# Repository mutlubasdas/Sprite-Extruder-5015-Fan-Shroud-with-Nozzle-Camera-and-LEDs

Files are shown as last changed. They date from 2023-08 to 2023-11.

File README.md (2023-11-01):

Sprite extruder is pretty good but the cooling is just not good enough!

So I did some research, got inspired by a couple of models and made my own.

Since I was making my own, I thought I make it a bit extra.

I always wanted to have a nozzle cam so I designed the shroud around it.

I'm using a [OV5640 camera](https://www.aliexpress.us/item/3256804790797706.html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) with autofocus, since that has a smaller package. The video is stable, I'm not getting any flickering, maybe I just got lucky with it :)

The focal length is more than 20mm with this camera so I used this [macro lens](<a target="_blank" href="https://www.amazon.com/gp/product/B08MFSDZB8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">Blips Macro Plus Lens</a>)* to achieve the shooting distance required! I cut it down the same size of the camera and just placed it in front of it, it sits just well because left some clearance for it in the model. Shoutout to [chilicoke](https://github.com/chilicoke) for finding that macro lens. He has an awesome [video](https://www.youtube.com/watch?v=GAp23w_dnNc&t=65s) for his own Voron nozzle camera mod.

   * I know this item has been out of stock but the seller on amazon said they'll restock in     October 2023.

    * Just checked today (11/1/23) and it's in stock right now. And created an affiliate link for the item.

There's a bracket next to the fan for the camera PCB. I used [M1.6 heatset](https://www.aliexpress.us/item/3256804538587668.html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) insert and screws to mount it.

And obviously I needed light to see what I'm printing so I added two tiny LEDs, I had extra [WS2813 LEDs](https://www.digikey.com/en/products/detail/seeed-technology-co-ltd/601000200/8120706) around so I used them but I think other models may fit also If they have similar size. Please refer to the spec sheet for details on wiring for your choice of LEDs.

Soldering was a pain the back for me! I'm not a pro at it. It took me a while and I think I killed two LEDs in the process but I eventually got it :) I also added some cable management clips on both arms of the shroud. Be gentle with them and they work, otherwise you might break them.

Finally just throw in a good 5015 fan, I got [this one](https://www.filastruder.com/products/delta-bfb0524hh-blower-fan) from Filastruder. I also made some holes that goes to the camera and the LEDs, hoping that it might help with their cooling? :) Not 100% sure how much that affects to be honest because I was lazy to test with and without them but I wanted to be safe and give them some airflow too! :) They also have holes at the bottom and they're for making disassembly easy if ever needed.

I printed with ABS, with 0.2 layer height, with a self made chamber and I used a bit of fan starting from layer 10+, which makes the print have good detail and helps with some of the small overhangs. I didn't use supports and I think you should be able to print without supports as well. Also I'd suggest considering the thermal shrinkage when printing it, I scaled my model 0.6 % in XY and %0.2 in Z. Obviously don't just copy my numbers, yours will be different depending on material, slicer settings, cooling, printer environment etc.

Anyways, enough talk, I hope some of you find it useful and make your own. It's a very dangerous project though, because once you have it working you get addicted to watching it!! :)

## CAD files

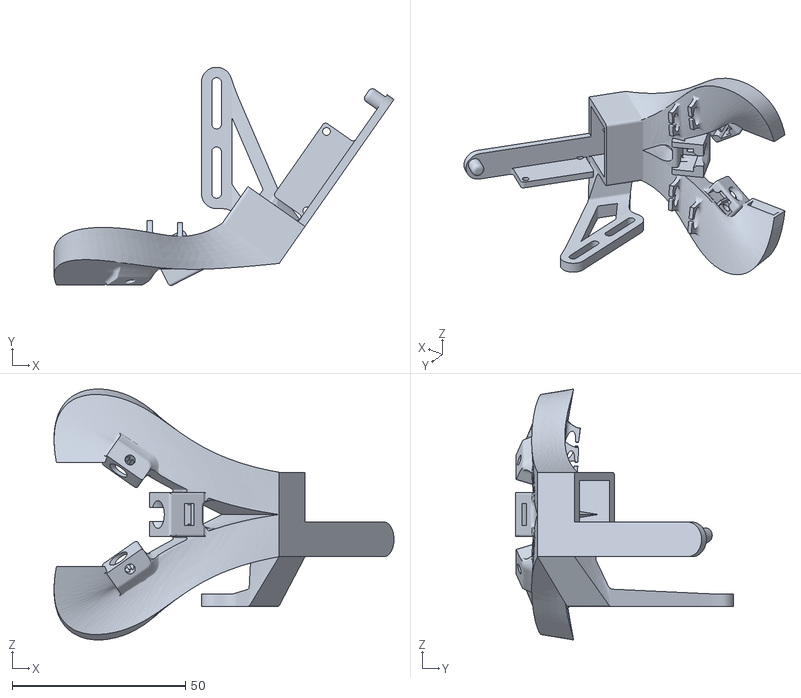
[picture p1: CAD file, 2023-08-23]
Sprite Extruder 5015 Fan Shroud with Nozzle Camera and LEDs.stl
98.1 x 63.0 x 72.4
